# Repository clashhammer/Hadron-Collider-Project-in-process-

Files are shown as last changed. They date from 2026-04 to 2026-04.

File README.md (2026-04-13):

# Hadron-Collider-Project-in-process-
A project that simulates how a particle moves in a hadron collider by spinning a metal ball inside a ring and is being pushed by electromagents.

This is one of my hardest projects so far, since it has been so prolongued and at the same time very resourse and time consuming. It is by now almost ready and soon me and my friend are going to finish it, but just so it doesn't stay untouched in my project library I will ship it and continue on later. :)

Anyways, since I saw the "physics lab" sidequest I decided to describe what me and my friend have calculated and how our project works and what it showcases.

PLAN OF THE PROJECT:
- The project revolves around hadron colliders. The idea is to showcase how they work, what they do and why do they do it. So a hadron collider is essentially a giant circle (the biggest right now is in CERN in Switzerland which is about 27km (~16.6 miles) in lenght, but in the USA there is a plan to make one that is about 100km (~62 miles) in lenght), that has a bunch of electromagnets. The point of these electromagnets is to push subatomic particles (protons, electrons and neutrons) to near lightspeed and collide them with eachother, hence why's it called a hadron collider. The idea of colliding these particles is to learn about fundamental particles, forces and events near the Big Bang that created the universe. Interesting fact is that the large hadron collider in CERN uses about 1.3 TERRAwatts of power annually which is enough to power 370,000 european households for a whole year (which is crazy to think about). 

THEORETICAL AND EXPERIMENTAL CONCLUSIONS OF OUR PROJECT:
- Thus far we have made a lot of calculations and our plan is flawless. We have concluded that a coil with less windings (about 150-180) is best for the induction (how fast electricity flows through the coil) and thus for the impulse power of the coil. The induction has to be very high so that the ball gets pushed with greater force and thus being faster. We have concluded with an experiment with a single coil and board that this is the best amount of windings. We have calculated the maximum speed + the timings of the coils. With the best timing and counting friction the maximum speed of the ball should be 7,3-7.4 m/s or about 24,3 ft/s. With slightly worse timing and counting friction we get about 4,8 m/s or about 15,8 ft/s. With the worst timing and counting friction we get 2 - 4 m/s or 6,6 - 13,1 ft/s. And you might ask what are these timings. Well the timings are the time between the coil powering on and the induction being at maximum. Since we use IR emmiter and receiver on the boards so that the coils aren't always activated so that they are not overheating, and have impulses of magnetic fields, we calculated that the time between the IR light being obstructed by the ball and the coil being at it's maximum induction and therefore the best timing is when the ir sensors are 1,5cm away from the CENTER of the coil. Finnaly we have calculated that each coil needs about 1,5A of current to operate propperly. That means that to finish this project I need to buy a charger that is at least 6A to support those 8 coils. More on that when we finish the project.

Here is a picture of the pcb schematic if you decide to make one of your own. There you can see all resistor values and stuff you need for the boards as well as where to place it. You can get the pcb files from the files and get it printed yourself by PCBWay or JLCPCB (That's what I use).


Shout out to my friend who made most of the calculations. He wants to be a theoretical physicist and knows a lot about how to calculate the stuff we needed to be calculated for this project. I was more on the practical and cirquitry side, gathering all the parts for the project, making a pcb design, making schematics and so on. 

Anyways, I'll redact this once the project is finally ready. Until then goodbye!

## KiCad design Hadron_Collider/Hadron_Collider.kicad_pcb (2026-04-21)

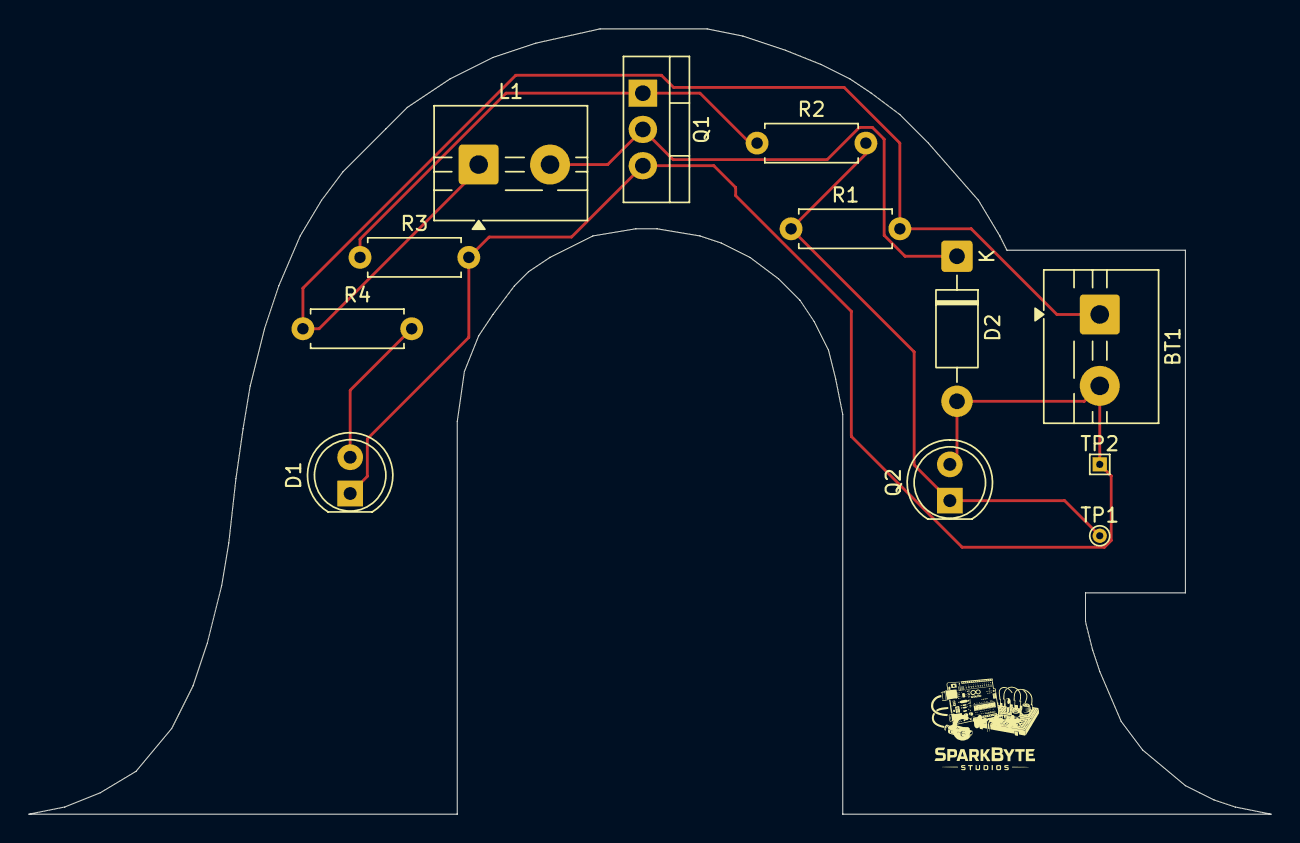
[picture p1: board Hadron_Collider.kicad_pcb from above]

Board: 2 copper layers, 87.0 x 55.0 mm, 12 parts (0 on the bottom side), 6 nets.

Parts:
BT1: 12V, 2A; TerminalBlock_MaiXu_MX126-5.0-02P_1x02_P5.00mm
D1: LD271; LED_D5.0mm_Clear
D2: 1N4007; D_DO-41_SOD81_P10.16mm_Horizontal
L1: L; TerminalBlock_MaiXu_MX126-5.0-02P_1x02_P5.00mm
Q1: IRLZ44N; TO-220-3_Vertical
Q2: BPW40; LED_D5.0mm_Clear
R1, R3: 10KΩ; R_Axial_DIN0207_L6.3mm_D2.5mm_P7.62mm_Horizontal
R2: 47Ω; R_Axial_DIN0207_L6.3mm_D2.5mm_P7.62mm_Horizontal
R4: 220Ω; R_Axial_DIN0207_L6.3mm_D2.5mm_P7.62mm_Horizontal
TP1: TestPoint; TestPoint_THTPad_D1.0mm_Drill0.5mm
TP2: TestPoint; TestPoint_THTPad_1.0x1.0mm_Drill0.5mm

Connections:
unnamed: BT1.1 (+), L1.1, R1.2, R4.1
unnamed: BT1.2 (-), D1.1 (K), D2.2 (A), Q1.3 (S), Q2.2 (E), R3.2, TP2.1
unnamed: D1.2 (A), R4.2
unnamed: D2.1 (K), L1.2, Q1.2 (D)
unnamed: Q1.1 (G), R2.1, R3.1
unnamed: Q2.1 (C), R1.1, R2.2, TP1.1

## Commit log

2026-04-11 Schematic and PCB design for the coil boards.
2026-04-21 Files (schematic, pcb and gerber)
    [Hadron_Collider-B_Cu.gbr, Hadron_Collider-B_Mask.gbr, Hadron_Collider-B_Paste.gbr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]
